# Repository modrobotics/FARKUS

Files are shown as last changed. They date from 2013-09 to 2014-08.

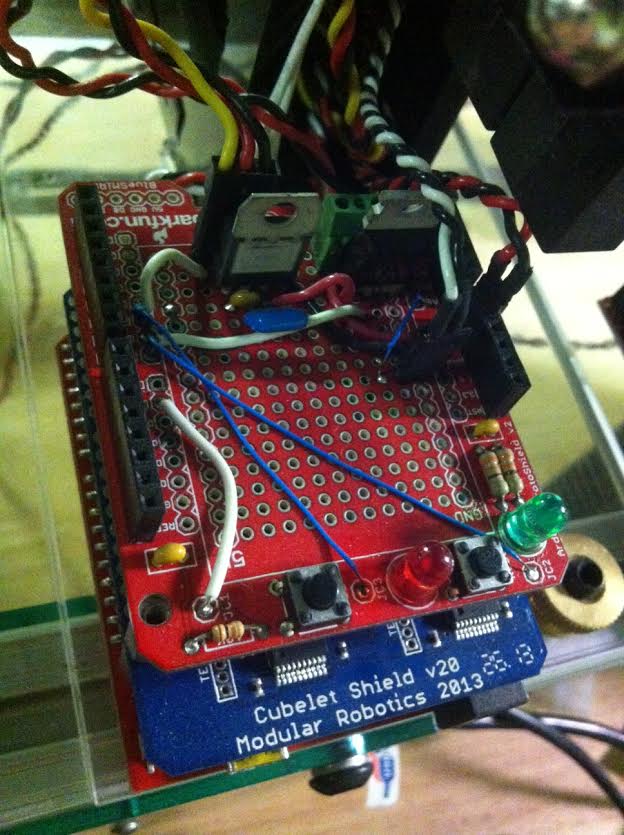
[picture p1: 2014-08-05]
FARKUS Bench/Modules/Comm Tester/Electronics/comm-board.jpg

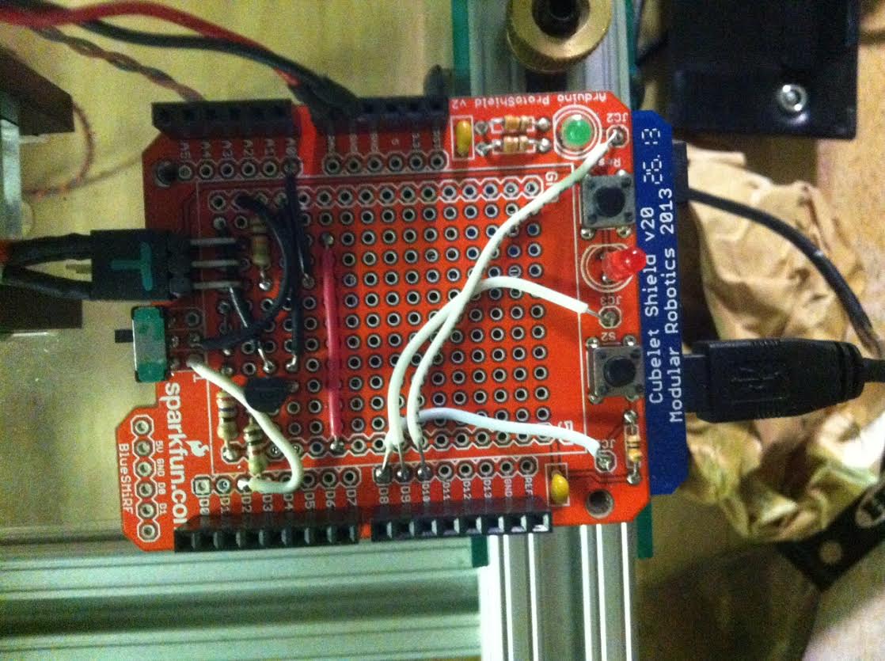
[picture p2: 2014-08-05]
FARKUS Bench/Modules/Flashlight-Brightness Module/Electronics/FBM-board.jpg

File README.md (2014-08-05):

FARKUS is an open source robotic construction kit for factory automation.
======

At Modular Robotics, we make robot construction kits for kids in our factory in Boulder, CO. Lots of people think this is batshit-crazy; toys are made in China. In order to stay cost-competitive, we do a lot of robotization and automation, but not just by buying a bunch of robot arms. Instead of buying hundred thousand dollar industrial robots and PLCs, we've been making our own industrial robots with 3D printed and laser cut parts and Arduinos.

FARKUS is more than an assembly robot, it's an ecosystem of simple robots that work together. In the same way that our commercial products are made out of lots of tiny robots, the power of FARKUS lies in the modularity and interconnection between various modules that can be reconfigured quickly to support different assembly processes and production lines.

At a basic level, a factory performs a bunch of operations to a bunch of products. The Modular Robotics factory, for instance, uses operations like soldering, ultrasonic welding, programming, testing, and printing to make products like Cubelets and MOSS. FARKUS consists of several parts: movers, to move products through the factory; a collection of modules that perform operations to the products; a control system to manage the ecosystem; and nests to cradle the products as they make their way through a production line.

This repository is pretty rough -- we've dumped files here with only minimal documentation.  We'll update as we make progress and we hope that others will contribute and document.  For now, there are a bunch of Solidworks, Eagle, and code files to peruse along with a few readmes.

More info and media on the wiki at: www.farkus.org

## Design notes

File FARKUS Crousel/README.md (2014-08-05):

FARKUS Crousel
======

The Crousel is a mechanism for pogo-testing and/or programming 60 small circuit boards without human intervention.

The hardware folder contains the master solidworks assembly (master.sldasm) which references all other solid parts.

The software folder contains the arduino sketch for the crousel and the firmware for an example flashing module.

The electronics folder contains a fritzing diagram for wiring up a crousel and an example layout for a flashing module.

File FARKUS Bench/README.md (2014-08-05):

FARKUS Bench
======

The FARKUS Bench is an assembly of interconnected modules that work together to complete a set of tasks. We use the Bench to test Cubelets.

The Bench comprises the physical Table, the Conveyance, and Modules, along with the Cubelet Holder (which is a type of FARKUS Nest) and some electrical interfaces.

The Table is the mechanical substrate to which Modules and the Conveyance are fixed. Modules are the units that perform tasks, and the Conveyance is a device that advances workpieces (Cubelets, in our case) through the Modules. The Cubelet Holder is a Nest that has been specifically designed to attach Cubelets to the Conveyance, and the electrical interfaces allow Modules to easily connect up to the Table and communicate with one another.

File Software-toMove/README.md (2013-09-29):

FARKUS Desk
======

This software supports Modular Robotics' FARKUS Table.  It is designed to be
run on a Raspberry Pi, and has been optimized for use on that platform.  That
said, all of the code is cross-platform compatible and (with some minor modifications*)
you'll be running on Windows.

Assuming you're not trying to state your love for Windows by using an open source
factory automation project, here's how you'll get your Pi set up to use FARKUS Desk.

1. Start from a vanilla distro of Raspbian.  Download from: http://downloads.raspberrypi.org/raspbian_latest 
2. Get apt-get up-to-date:
        
        sudo apt-get update
        
3. Install wxPython 2.8 for Python 2.7 (Python 2.7 itself is installed by default):
        
        sudo apt-get install python-wxgtk2.8 python-wxtools wx2.8-i18n libwxgtk2.8-dev
        
4. Install pyserial.

        cd ~
        wget https://pypi.python.org/packages/source/p/pyserial/pyserial-2.6.tar.gz
        tar -xvf pyserial-2.6.tar.gz
        cd pyserial-2.6
        python ./setup.py install
        
5. Install git

        sudo apt-get install git
        ssh key-gen -t rsa -C "[your email here]"
        
6. There are some statically-defined file paths in this code.  Please clone this repo to ```/home/pi/FARKUS```

        cd /home/pi
        git clone https://github.com/modrobotics/FARKUS.git
        
7. Adjust permissions to allow execution

        sudo chmod o+x /home/pi/FARKUS/python/FarkusDesk.py
        
8. Run Desk.

        /home/pi/FARKUS/run.exe
        
9. Profit!

* The cross-platform capability of the serial device discovery functionality
  is currently statically coded to support UNIX/Mac.  Some commenting/uncommenting
  is all that is required to switch to Windows.

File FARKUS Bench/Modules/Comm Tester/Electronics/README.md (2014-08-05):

Comm board
======
This simple board provides utility functions for the Cubelet communication test. Two MOSFET switch circuits are used to control two pneumatic solenoids that raise and lower the arm. The board also breaks out power connections and servo connections for the end-effector servos.

The two buttons are included in the Sparkfun protoshield kit. One button is used as a reset, the other button starts the test manually. The red and green LEDs indicate fail or pass result of most recent test.

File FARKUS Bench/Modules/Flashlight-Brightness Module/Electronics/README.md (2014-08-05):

FBM-board
======
This is a photograph of the prototype board for the flashlight-brightness tester. This circuit is relatively simple, comprising:
-A switch, to manually swap between flashlight and brightness modes (this is also switchable using serial comm)
-A voltage divider circuit including the photocell to measure flashlight brightness
-A BJT circuit to switch the ultra-bright LED used to test the brightness cubelet.

The two buttons are included with the protoshield kit. One is used as a reset button, the other is to manually start the test. The red and green LEDs indicate fail or pass result of most recent test.

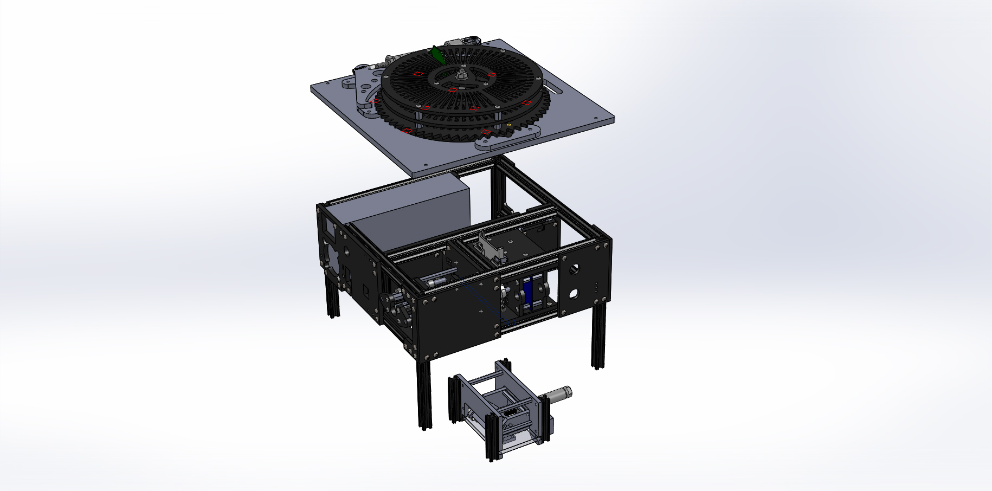
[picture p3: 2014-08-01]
FARKUS Crousel/Hardware/Images/Explode1.JPG

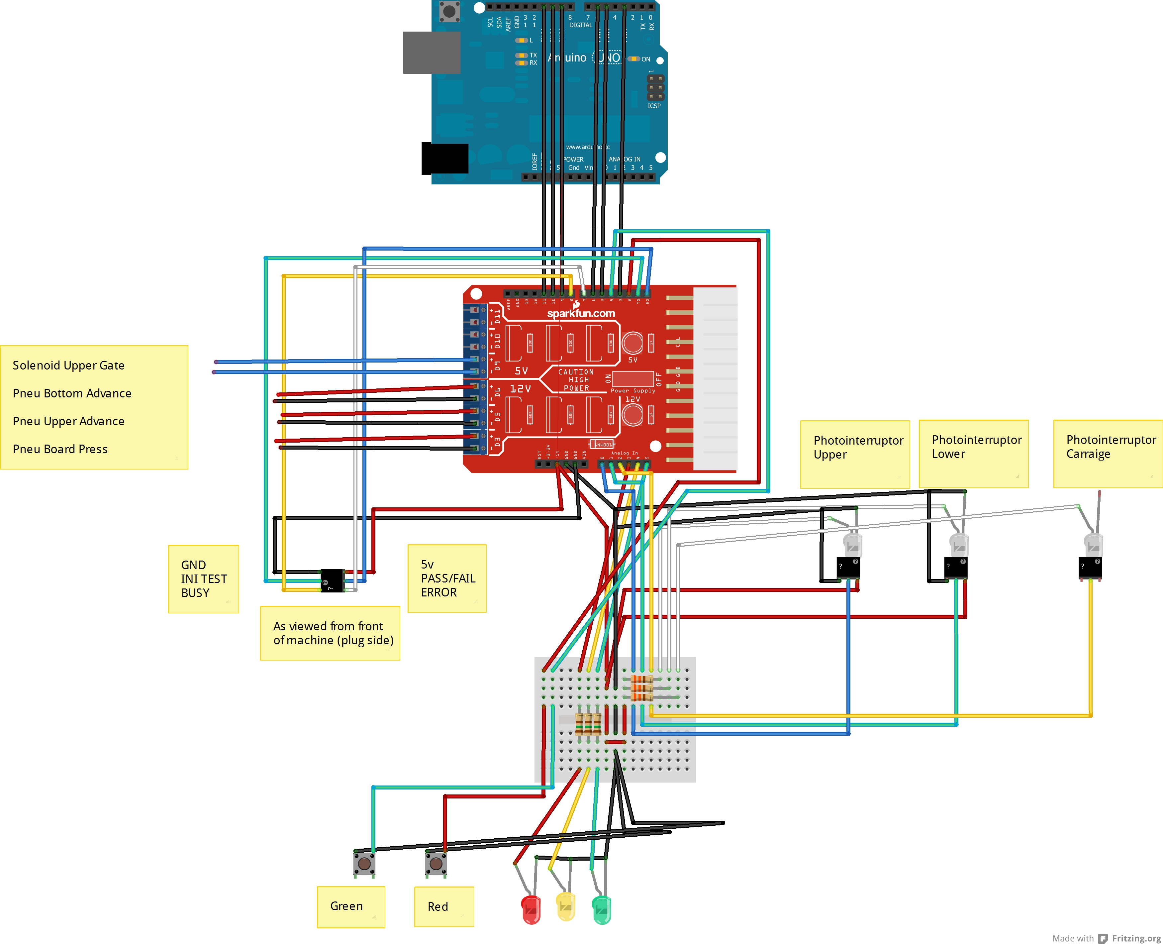
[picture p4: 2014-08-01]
FARKUS Crousel/Hardware/Images/Schematic.jpg

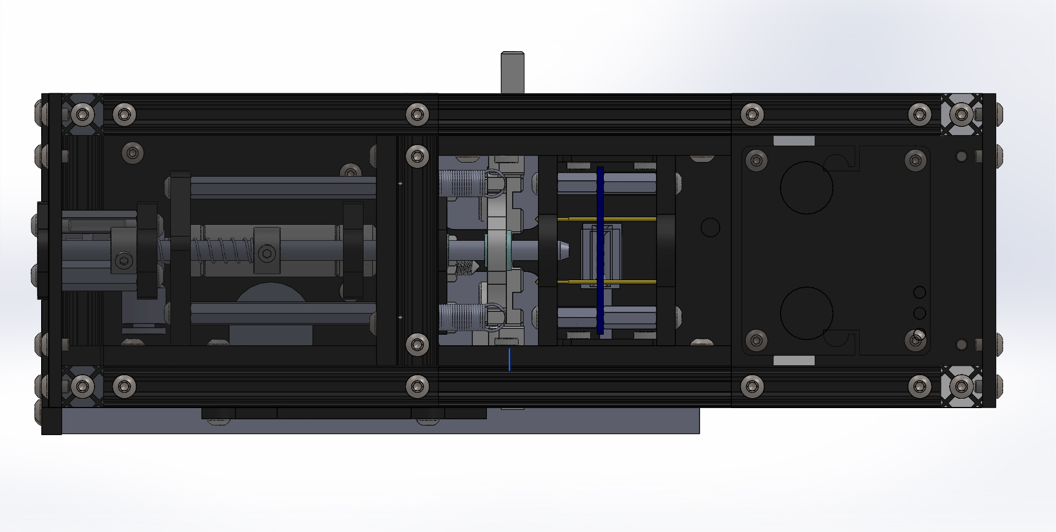
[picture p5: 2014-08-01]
FARKUS Crousel/Hardware/Images/Main1.JPG

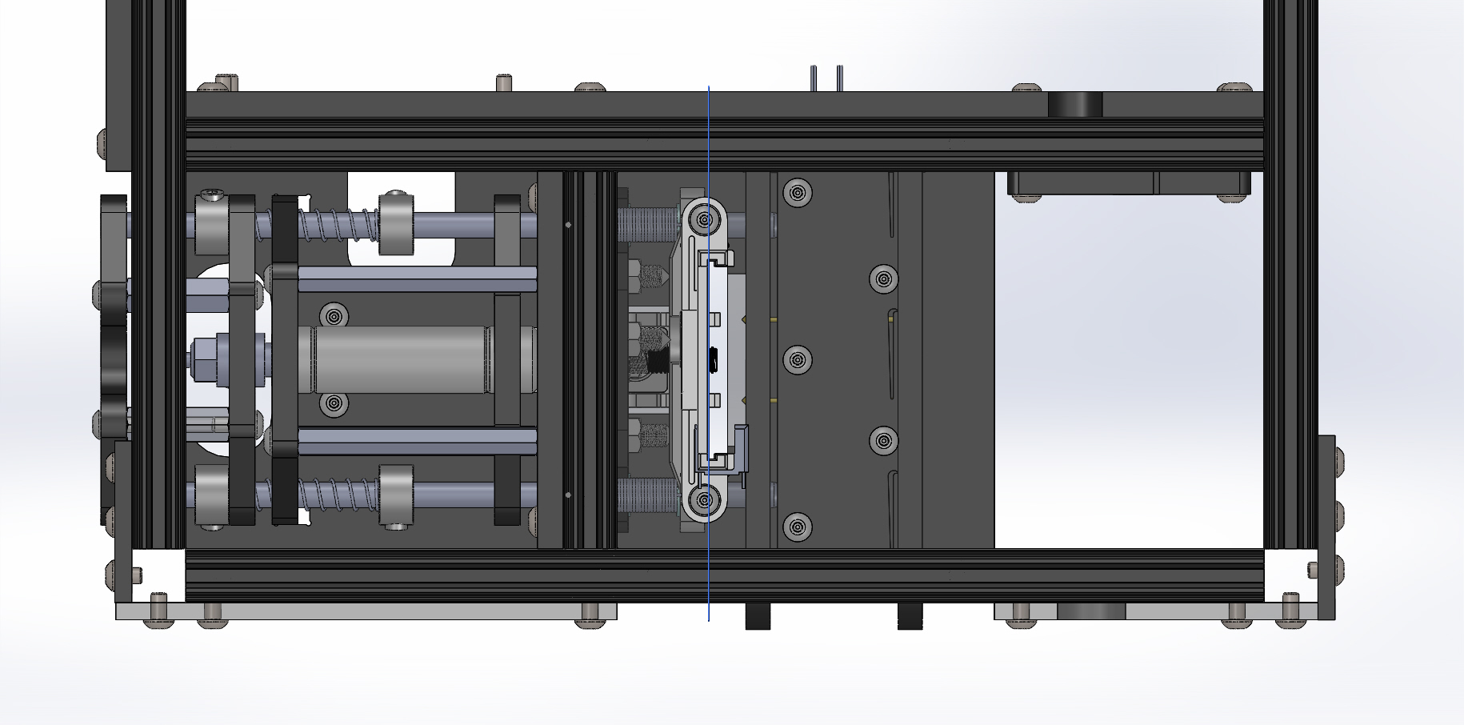
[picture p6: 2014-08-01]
FARKUS Crousel/Hardware/Images/Main2.JPG

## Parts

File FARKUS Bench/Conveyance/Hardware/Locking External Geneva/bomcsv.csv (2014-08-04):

ITEM NO. | PART NUMBER | DESCRIPTION | QTY.
1 | genevaSprocket |  | 2
2 | lockCrank |  | 2
3 | lockWheel |  | 2
4 | driveCrank |  | 1
5 | frontPlate |  | 1
6 | 57155K305 |  | 4
7 | fenderShim-0.025 |  | 8
8 | 97395A410 |  | 2
9 | 93365A110 |  | 4
10 | 90273A070 |  | 4
11 | 97395A401 |  | 4
12 | longBearing | McMaster Part # 6621K75 | 1
13 | 99040A510 | McMaster Part # 93268A509 | 2
14 | wheelSpacer |  | 2
15 | 94773A770 |  | 2
16 | 93985A534 |  | 2
17 | 92474A117 |  | 1
18 | 91124A160 |  | 2
19 | MirrorfrontPlate |  | 1
20 | 94035A581 |  | 1
21 | 93298A108 |  | 1
22 | Inch - Spur gear 24DP 66T 14.5PA 0.125FW ---S66N3.0H2.0L0.1875N |  | 1
23 | Inch - Spur gear 24DP 24T 14.5PA 0.125FW ---S24N3.0H2.0L0.1875N |  | 1
24 | 2453K31 |  | 1
25 | 91780A167 |  | 2
26 | 92474A456 |  | 1
27 | 90275A192 |  | 2
28 | 92949A111 |  | 4
29 | HX-SHCS 0.073-72x0.5x0.5-N |  | 3
30 | 1103 | Pololu Part # 1103: 29:1 Metal Gearmotor 37Dx52L mm | 1
31 | motorMountPlate |  | 1
32 | 91780A162 |  | 3
33 | 92949A106 |  | 15
34 | 92949A108 |  | 3
35 | 91239A113 |  | 6
36 | Final |  | 1
37 | RS485Breakout |  | 1
38 | 93365A120 |  | 8
39 | 93505A430 |  | 8
40 | Part26^HDLayout |  | 1

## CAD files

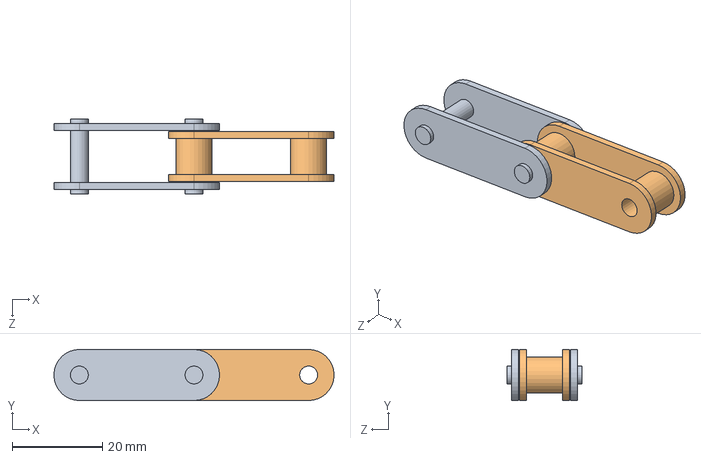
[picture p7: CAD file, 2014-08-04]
FARKUS Bench/Conveyance/Hardware/Locking External Geneva/Chain/linkPair.SLDASM
62.1 x 11.3 x 16.5 mm
bigLink
smallLink

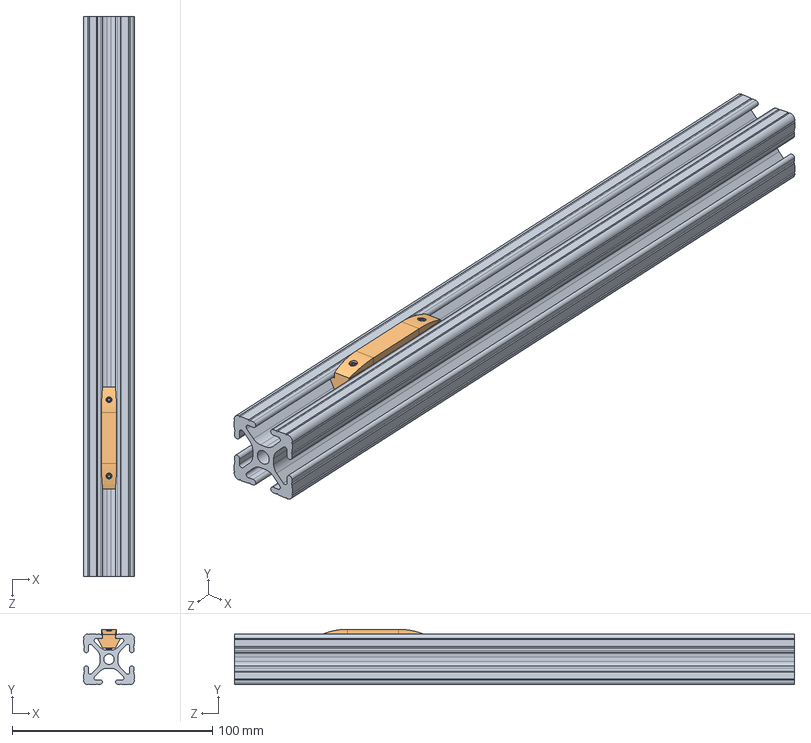
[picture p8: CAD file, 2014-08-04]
FARKUS Bench/Conveyance/Hardware/Riser/riserwithbeam.SLDASM
25.4 x 27.7 x 279.4 mm
47065T209-4SS-11IN
92395A315 x 2
94355A141 x 2

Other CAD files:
FARKUS Bench/Conveyance/Hardware/Locking External Geneva/MirrorFinal.sldasm
FARKUS Bench/Conveyance/Hardware/Locking External Geneva/User Library-QFN32 (FTDI)_Default_1.sldasm
FARKUS Bench/Conveyance/Hardware/Locking External Geneva/User Library-ALU-D8_Default_1.sldasm
FARKUS Bench/Conveyance/Hardware/Locking External Geneva/1103.SLDPRT
FARKUS Bench/Conveyance/Hardware/Locking External Geneva/3088A429.SLDPRT
FARKUS Bench/Conveyance/Hardware/Locking External Geneva/57155K305.SLDPRT
FARKUS Bench/Conveyance/Hardware/Locking External Geneva/57485K660.SLDPRT
FARKUS Bench/Conveyance/Hardware/Locking External Geneva/6409K150.SLDPRT
FARKUS Bench/Conveyance/Hardware/Locking External Geneva/90273A070.SLDPRT
FARKUS Bench/Conveyance/Hardware/Locking External Geneva/90274A126.SLDPRT
FARKUS Bench/Conveyance/Hardware/Locking External Geneva/90275A192.SLDPRT
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

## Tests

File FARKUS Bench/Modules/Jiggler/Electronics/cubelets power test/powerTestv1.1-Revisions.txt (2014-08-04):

screw terminal silkscreen must be moved

optical relay land pattern must be narrowed

arduino shield silkscreen must be moved on side with power resistor

add status LEDs for power on and each face active.

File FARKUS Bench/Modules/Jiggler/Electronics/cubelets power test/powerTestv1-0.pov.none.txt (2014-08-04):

Parts not found in 3dpack.dat or 3dusrpac.dat are:
//D1	B340A	B340A
//L1	ELL6UH120M	ELL6UH120M
//R1	6.6	AXIAL-0.8
//R2	1k	0603-RES
//R3	1k	0603-RES
//R4	1k	0603-RES
//R5	1k	0603-RES
//R6	TRIMPOT-2	TRIMPOT_TC33
//TP1	TEST-POINT3X5	PAD.03X.05
//U$3	ARDUINO_R3_SHIELD	UNO_R3_SHIELD
//U1	SI1553DL-T1-GE3	SOT65P210X110-6N
//U2	SI1553DL-T1-GE3	SOT65P210X110-6N
//U3	SI1553DL-T1-GE3	SOT65P210X110-6N
//U4	SI1553DL-T1-GE3	SOT65P210X110-6N
//U5	SI1553DL-T1-GE3	SOT65P210X110-6N
//U6	LM311DG	SOIC127P600X175-8N
//U7	FAN8303MX	FAN8303MX

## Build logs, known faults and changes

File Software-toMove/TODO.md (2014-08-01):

MUST HAVE TODO
#######################
*Proper response handling on serial workers, sending back error code (Moyes)
*Dumb emercency stop (Moyes) - Part received. 
*Hookup "parts" type menu (Moyes)
*Flashing modules final bugfix(s)  (Moyes)
*Automatic advance / preventing premature advancement (Moyes)
*Arm position detection, state status reporting (Nev)
*3D print 12 more part faces (Nev)
*~~fix double "GO" command bug~~ 
...then...

*characterize test: power (

++++++++++++++++++++++++
*smart emergency stop
*Update cubelets shieild
*Mechanical safety: EStop buttons, pinch point elimination/covers
*failure mode tracking
*make spare faces
*maintenance schedule: Tracking, alerts
touch screen

MISC TODO
########################

*Known issue: if only conveyance is connected, you won't be able to get to the
    conveyance's config window. which is fine, since there's nothing to do in there anyway
    
*FarkusTable state control system
*Functions to support  farkustesttype, required tests, etc
   - Control Module Actions
   - Update part status after
   - 
*Look for TODOs in code. Duh.
*Enums for Commands
*implement commands to getCurrentConfigState on modules
*Manager class/functions in FarkusTable to manage module location constraints (2 modules in 1 location, etc.)
*Click on part-> Part details window with tests to run, results, serial number, added date/time, etc
*Click on module-> Module details, config.  WE have basic config.  Add buttons/text for manual commands, status debug info
*Ensure everything is properly destroy()'d before close()---memory leak risk
*serial failures aren't properly updating the Statusbar..fix that.

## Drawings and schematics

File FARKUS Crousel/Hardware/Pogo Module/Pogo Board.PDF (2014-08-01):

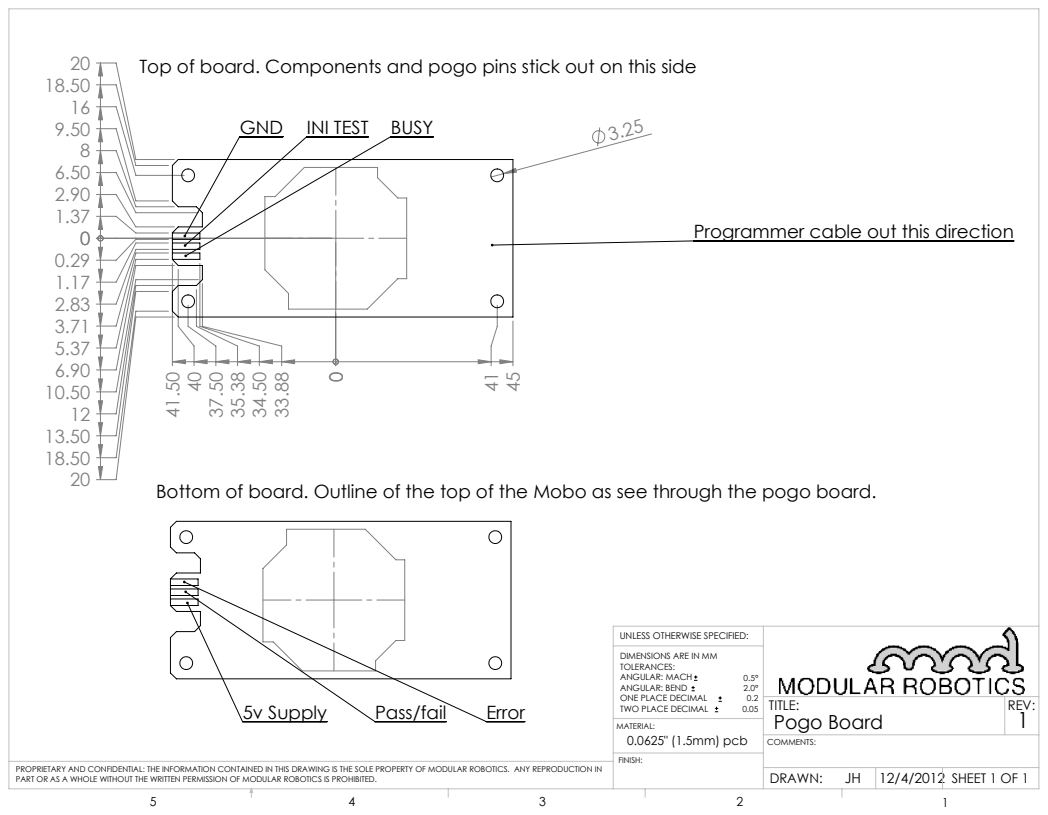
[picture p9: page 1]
5v Supply; Pass/fail; Error; Top of board. Components and pogo pins stick out on this side; SHEET 1 OF 1; DRAWN:; Pogo Board

GND INI TEST BUSY

Programmer cable out this direction

Bottom of board. Outline of the top of the Mobo as see through the pogo board.

UNLESS OTHERWISE SPECIFIED:
DIMENSIONS ARE IN MM
TOLERANCES:
ANGULAR: MACH
ANGULAR: BEND
ONE PLACE DECIMAL
TWO PLACE DECIMAL
MATERIAL:
0.0625" (1.5mm) pcb

PROPRIETARY AND CONFIDENTIAL: THE INFORMATION CONTAINED IN THIS DRAWING IS THE SOLE PROPERTY OF MODULAR ROBOTICS. ANY REPRODUCTION IN
PART OR AS A WHOLE WITHOUT THE WRITTEN PERMISSION OF MODULAR ROBOTICS IS PROHIBITED.

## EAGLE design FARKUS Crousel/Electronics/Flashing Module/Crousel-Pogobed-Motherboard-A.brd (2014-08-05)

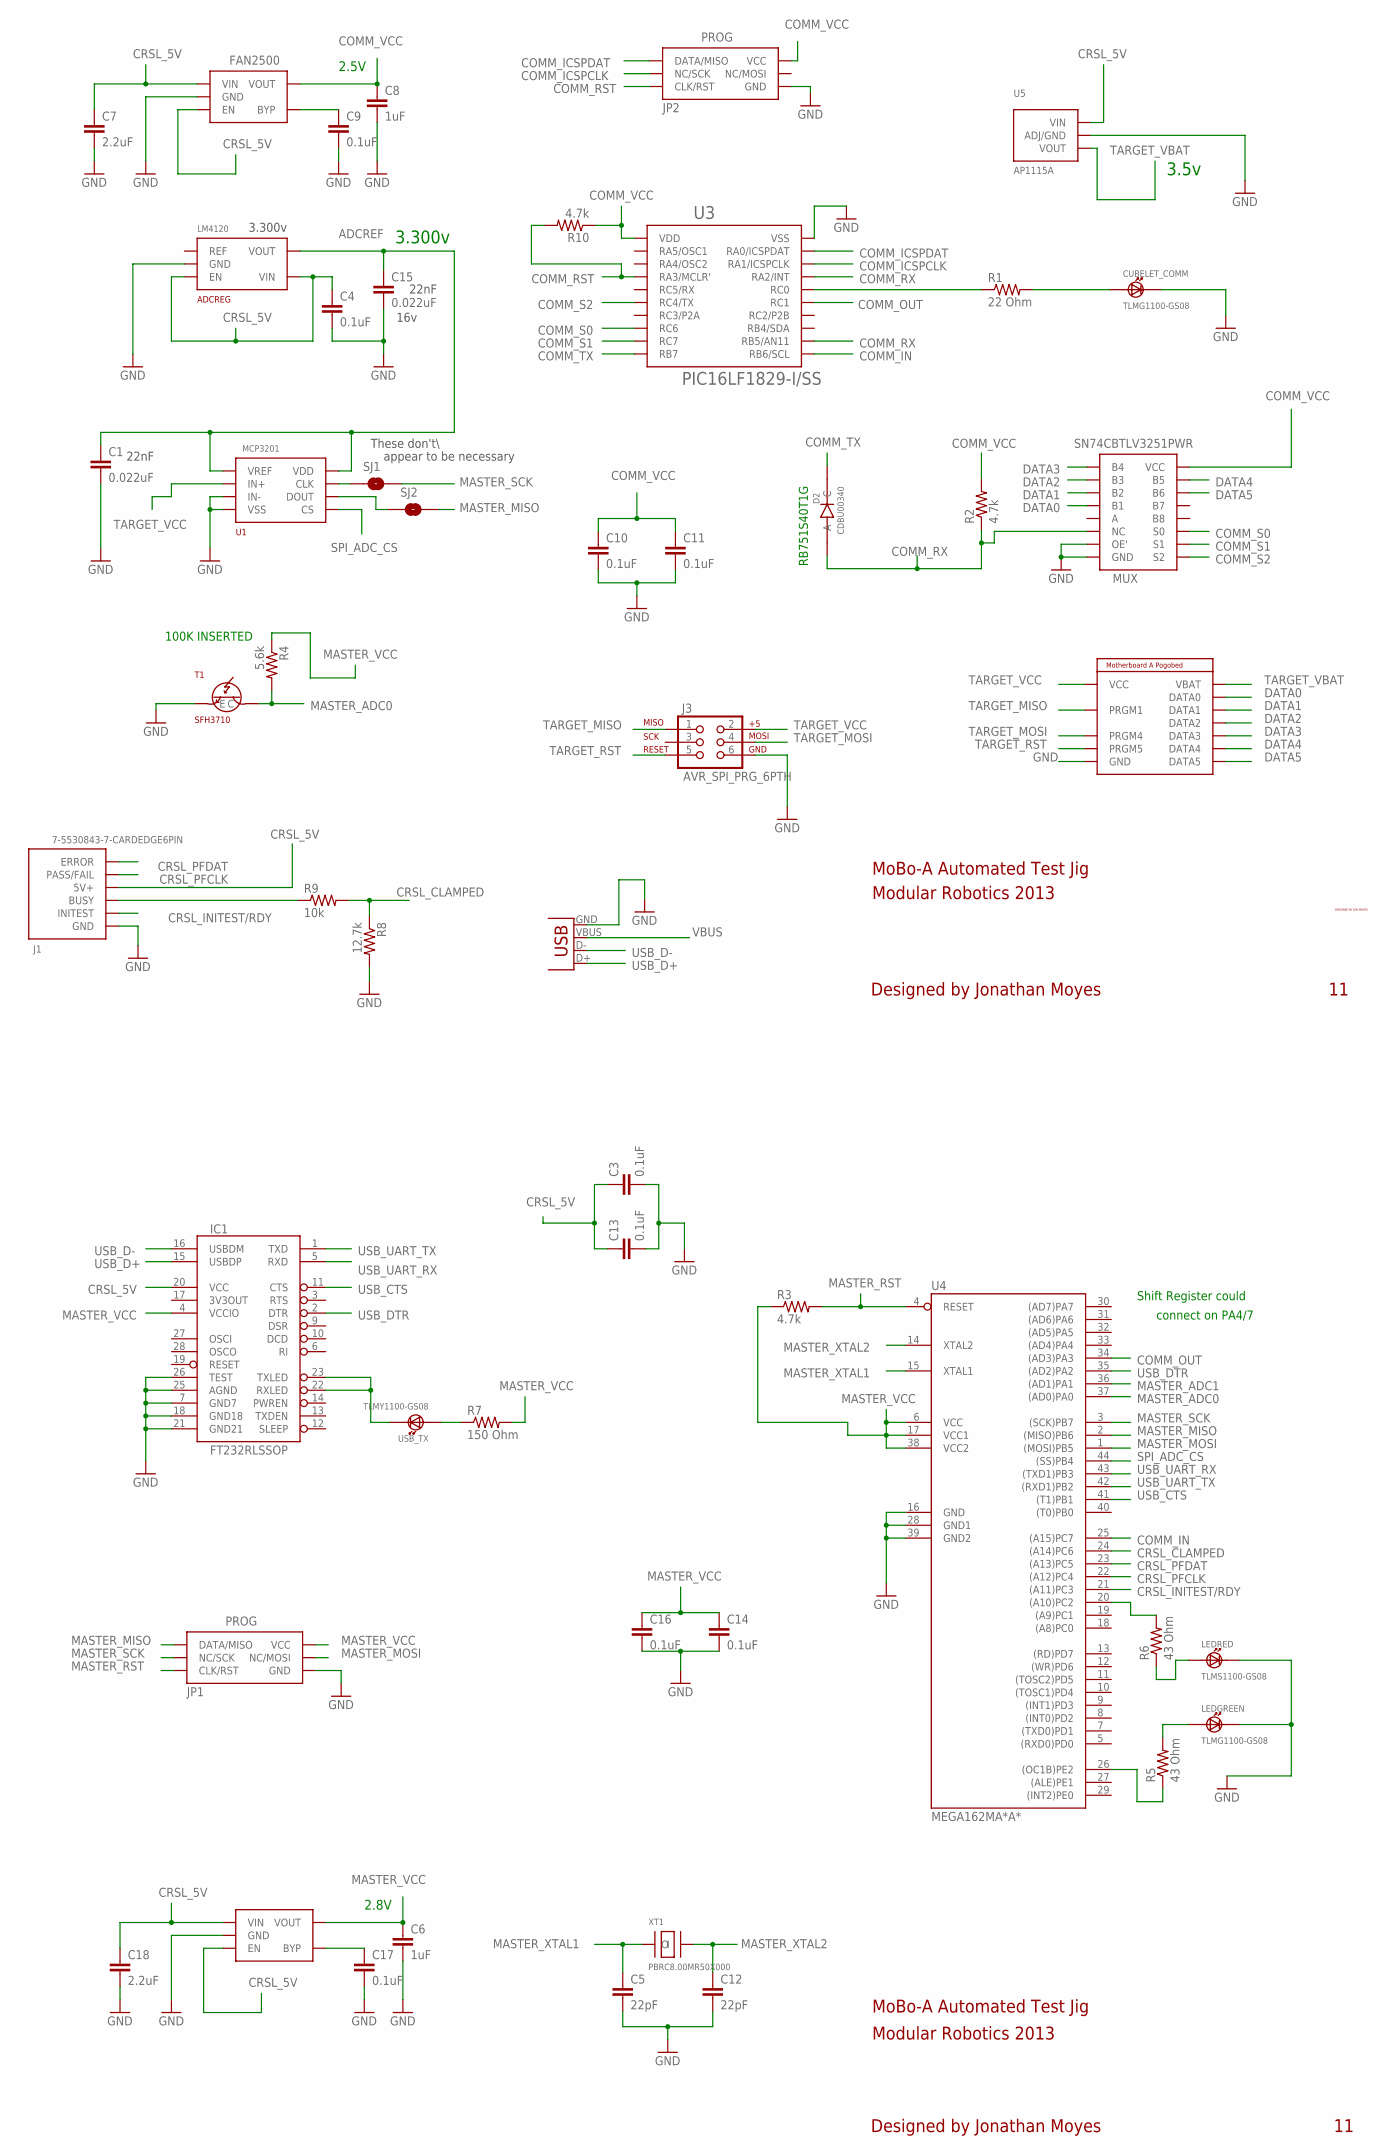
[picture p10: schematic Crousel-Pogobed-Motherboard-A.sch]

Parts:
2.8V: FAN2500
ADCREG: LM4120
C1, C15: 0.022uF; 0402-CAP
C3, C4, C9, C10, C11, C13, C14, C16, C17: 0.1uF; 0402-CAP
C5, C12: 22pF; 0402-CAP
C6, C8: 1uF; 0402-CAP
C7, C18: 2.2uF; 0402-CAP
COMMREG: FAN2500
CUBELET_COMM: TLMG1100-GS08; TLM*1100-GS08
D2: CDBU00340
IC1: FT232RLSSOP; SSOP28DB
J1: 7-5530843-7-CARDEDGE6PIN
J2: MOBOA
J3: AVR_SPI_PRG_6PTH; 2X3
JP1, JP2: PROG
LEDGREEN: TLMG1100-GS08; TLM*1100-GS08
LEDRED: TLMS1100-GS08; TLM*1100-GS08
MUX: SN74CBTLV3251PWR
R1: 22 Ohm; 0402-RES
R2, R3, R10: 4.7k; 0402-RES
R4: 5.6k; 0402-RES
R5, R6: 43 Ohm; 0402-RES
R7: 150 Ohm; 0402-RES
R8: 12.7k; 0402-RES
R9: 10k; 0402-RES
SJ1, SJ2: SOLDERJUMPERNO; SJ_2S-NO
T1: SFH3710
U1: MCP3201
U3: PIC16LF1829-I/SS
U4: MEGA162MA*A*; TQFP44
U5: AP1115A; SOT89
U$1: JON_MOYES_SIGNATURE
USB_TX: TLMY1100-GS08; TLM*1100-GS08
X1: USBPTH; USB-B-PTH
XT1: PBRC8.00MR50X000

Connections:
ADCREF: ADCREG.P$5 (VOUT), C1.1, C15.1, U1.P$1 (VREF), U1.P$8 (VDD)
COMM_ICSPCLK: JP2.P$3 (NC/SCK), U3.P$18 (RA1/ICSPCLK)
COMM_ICSPDAT: JP2.P$1 (DATA/MISO), U3.P$19 (RA0/ICSPDAT)
COMM_IN: U3.P$11 (RB6/SCL), U4.25 ((A15)PC7)
COMM_OUT: U3.P$15 (RC1), U4.34 ((AD3)PA3)
COMM_RST: JP2.P$5 (CLK/RST), R10.2, U3.P$4 (RA3/MCLR')
COMM_RX: D2.P$2 (A), MUX.P$6 (NC), R2.1, U3.P$12 (RB5/AN11), U3.P$17 (RA2/INT)
COMM_S0: MUX.P$11 (S0), U3.P$8 (RC6)
COMM_S1: MUX.P$10 (S1), U3.P$9 (RC7)
COMM_S2: MUX.P$9 (S2), U3.P$6 (RC4/TX)
COMM_TX: D2.P$1 (C), U3.P$10 (RB7)
COMM_VCC: C8.1, C10.1, C11.1, COMMREG.P$5 (VOUT), JP2.P$2 (VCC), MUX.P$16 (VCC), R2.2, R10.1, U3.P$1 (VDD)
CRSL_5V: 2.8V.P$1 (VIN), 2.8V.P$3 (EN), ADCREG.P$3 (EN), ADCREG.P$4 (VIN), C3.1, C4.1, C7.1, C13.1, C18.1, COMMREG.P$1 (VIN), COMMREG.P$3 (EN), IC1.20 (VCC), J1.P$4 (5V+), U5.3 (VIN)
CRSL_CLAMPED: R8.1, R9.2, U4.24 ((A14)PC6)
CRSL_INITEST/RDY: J1.P$2 (INITEST), U4.21 ((A11)PC3)
CRSL_PFCLK: J1.P$5 (PASS/FAIL), U4.22 ((A12)PC4)
CRSL_PFDAT: J1.P$6 (ERROR), U4.23 ((A13)PC5)
DATA0: J2.DATA0, MUX.P$4 (B1)
DATA1: J2.DATA1, MUX.P$3 (B2)
DATA2: J2.DATA2, MUX.P$2 (B3)
DATA3: J2.DATA3, MUX.P$1 (B4)
DATA4: J2.DATA4, MUX.P$15 (B5)
DATA5: J2.DATA5, MUX.P$14 (B6)
GND: 2.8V.P$2 (GND), ADCREG.P$2 (GND), C1.2, C3.2, C4.2, C5.2, C6.2, C7.2, C8.2, C9.2, C10.2, C11.2, C12.2, C13.2, C14.2, C15.2, C16.2, C17.2, C18.2, COMMREG.P$2 (GND), CUBELET_COMM.C, IC1.7 (GND7), IC1.18 (GND18), IC1.21 (GND21), IC1.25 (AGND), IC1.26 (TEST), J1.P$3 (GND), J2.PRGM6/GND (GND), J3.6, JP1.P$6 (GND), JP2.P$6 (GND), LEDGREEN.C, LEDRED.C, MUX.P$7 (OE'), MUX.P$8 (GND), R8.2, T1.E, U1.P$3 (IN-), U1.P$4 (VSS), U3.P$20 (VSS), U4.16 (GND), U4.28 (GND1), U4.39 (GND2), U5.2 (ADJ/GND), U5.2@1 (ADJ/GND), X1.GND
LED1: R6.2, U4.20 ((A10)PC2)
MASTER_ADC0: R4.2, T1.C, U4.37 ((AD0)PA0)
MASTER_ADC1: U4.36 ((AD1)PA1)
MASTER_MISO: JP1.P$1 (DATA/MISO), SJ2.2, U4.2 ((MISO)PB6)
MASTER_MOSI: JP1.P$4 (NC/MOSI), U4.1 ((MOSI)PB5)
MASTER_RST: JP1.P$5 (CLK/RST), R3.2, U4.4 (RESET)
MASTER_SCK: JP1.P$3 (NC/SCK), SJ1.2, U4.3 ((SCK)PB7)
MASTER_VCC: 2.8V.P$5 (VOUT), C6.1, C14.1, C16.1, IC1.4 (VCCIO), JP1.P$2 (VCC), R3.1, R4.1, R7.2, U4.6 (VCC), U4.17 (VCC1), U4.38 (VCC2)
MASTER_XTAL1: C5.1, U4.15 (XTAL1), XT1.I
MASTER_XTAL2: C12.1, U4.14 (XTAL2), XT1.O
unnamed: SJ1.1, U1.P$7 (CLK)
unnamed: R1.1, U3.P$16 (RC0)
unnamed: C9.1, COMMREG.P$4 (BYP)
unnamed: CUBELET_COMM.A, R1.2
unnamed: 2.8V.P$4 (BYP), C17.1
unnamed: IC1.22 (RXLED), IC1.23 (TXLED), USB_TX.C
unnamed: R5.1, U4.26 ((OC1B)PE2)
unnamed: R7.1, USB_TX.A
unnamed: LEDGREEN.A, R5.2
unnamed: J1.P$1 (BUSY), R9.1
unnamed: SJ2.1, U1.P$6 (DOUT)
unnamed: LEDRED.A, R6.1
SPI_ADC_CS: U1.P$5 (CS), U4.44 ((SS)PB4)
TARGET_MISO: J2.PRGM1, J3.1
TARGET_MOSI: J2.PRGM4, J3.4
TARGET_RST: J2.PRGM5, J3.5
TARGET_VBAT: J2.VBAT, U5.1 (VOUT)
TARGET_VCC: J2.PRGM2/VCC (VCC), J3.2, U1.P$2 (IN+)
USB_CTS: IC1.11 (CTS), U4.41 ((T1)PB1)
USB_D+: IC1.15 (USBDP), X1.D+
USB_D-: IC1.16 (USBDM), X1.D-
USB_DTR: IC1.2 (DTR), U4.35 ((AD2)PA2)
USB_UART_RX: IC1.5 (RXD), U4.43 ((TXD1)PB3)
USB_UART_TX: IC1.1 (TXD), U4.42 ((RXD1)PB2)
VBUS: X1.VBUS

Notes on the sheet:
16v
3.300v
2.5V
RB751S40T1G
2.8V
Shift Register could
connect on PA4/7
MoBo-A Automated Test Jig
Modular Robotics 2013
Designed by Jonathan Moyes
3.5v
22nF
These don't\
appear to be necessary
100K INSERTED

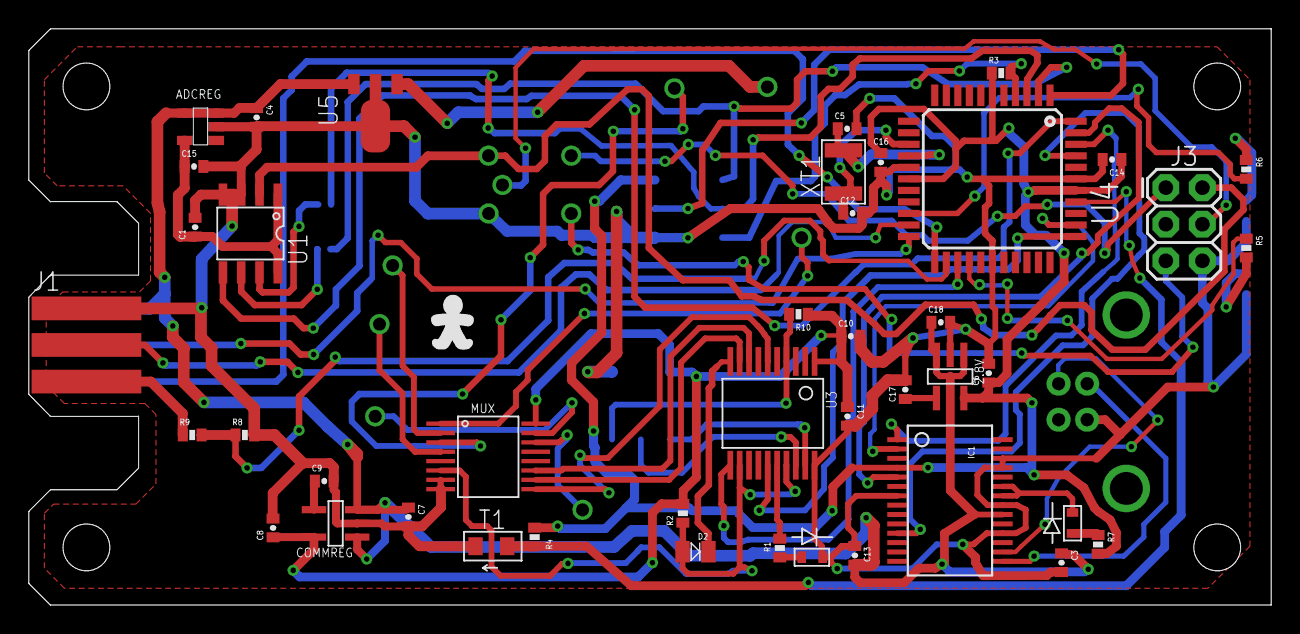
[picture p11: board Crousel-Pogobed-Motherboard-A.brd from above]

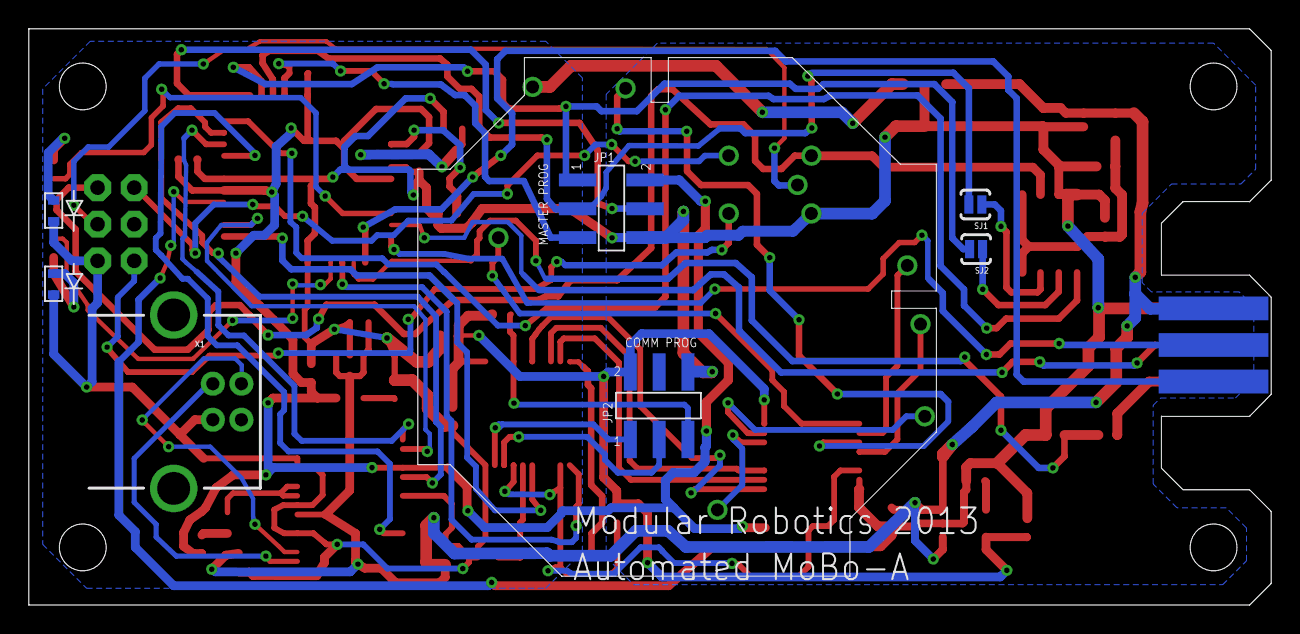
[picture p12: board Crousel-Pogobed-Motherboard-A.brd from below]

Board: 2 copper layers, 86.2 x 40.0 mm, 52 parts (8 on the bottom side), 57 nets.

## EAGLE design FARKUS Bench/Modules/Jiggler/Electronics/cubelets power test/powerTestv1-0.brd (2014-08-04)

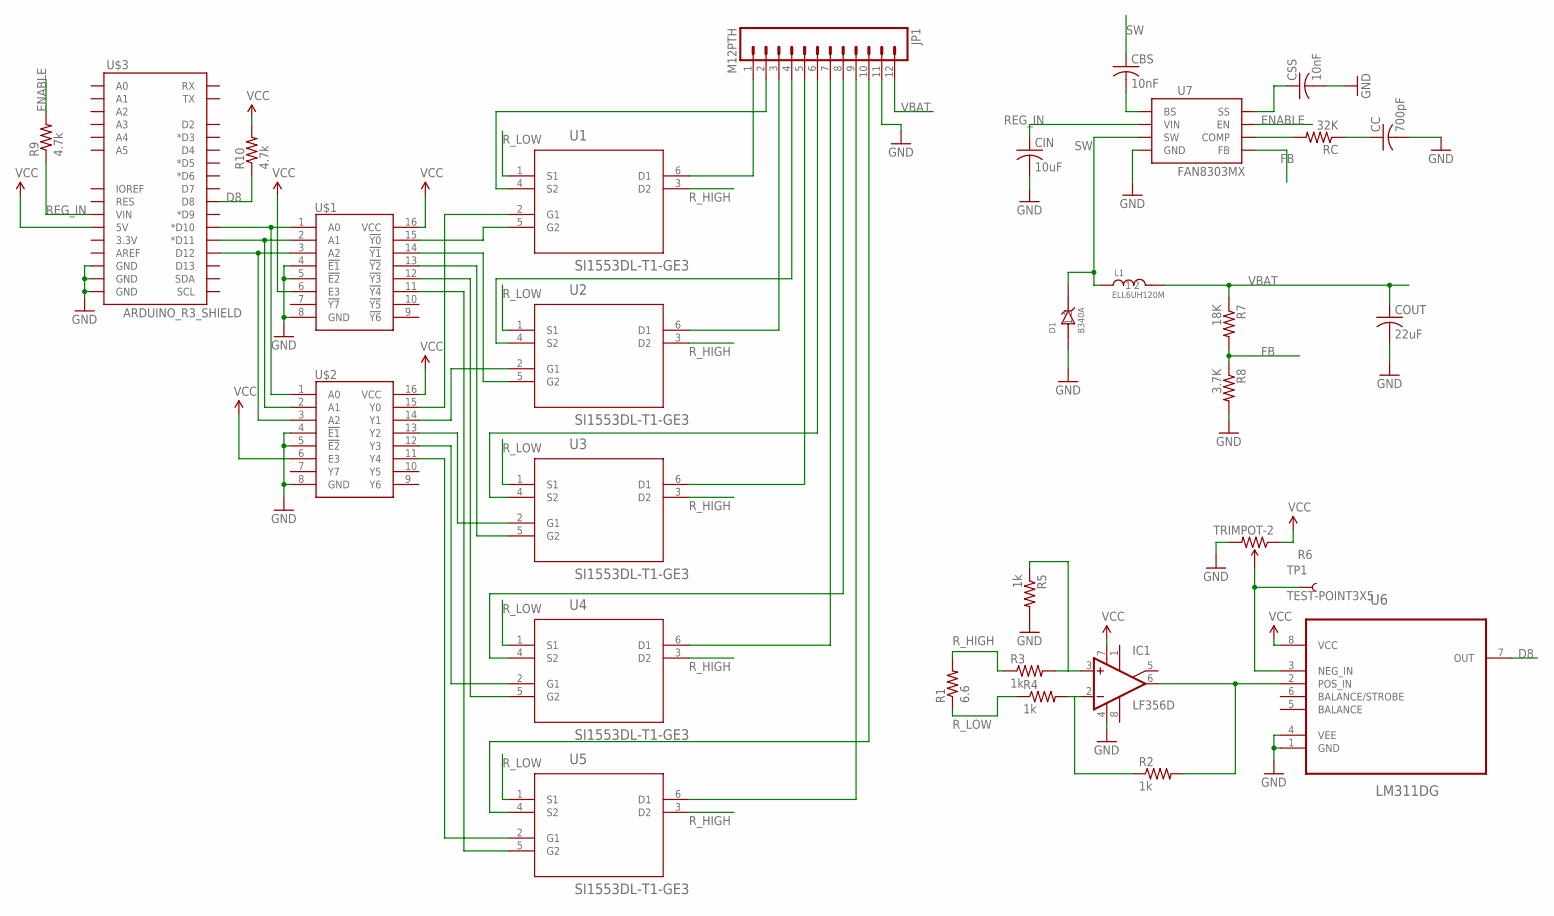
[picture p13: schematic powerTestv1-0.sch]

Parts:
CBS: 10nF; C0603
CC: 700pF; C0603
CIN: 10uF; C0603
COUT: 22uF; C0603
CSS: 10nF; C0603
D1: B340A
IC1: LF356D; SO08
JP1: M12PTH; 1X12
L1: ELL6UH120M
R1: 6.6; AXIAL-0.8
R2, R3, R4, R5: 1k; 0603-RES
R6: TRIMPOT-2; TRIMPOT_TC33
R7: 18K; R0603
R8: 3.7K; R0603
R9, R10: 4.7k; R0603
RC: 32K; R0603
TP1: TEST-POINT3X5; PAD.03X.05
U1, U2, U3, U4, U5: SI1553DL-T1-GE3; SOT65P210X110-6N
U6: LM311DG; SOIC127P600X175-8N
U7: FAN8303MX
U$1: 74HC138SO16; SO16
U$2: 74HC238SO16; SO16
U$3: ARDUINO_R3_SHIELD; UNO_R3_SHIELD

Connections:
D8: R10.1, U6.7 (OUT), U$3.D8
ENABLE: R9.2, U7.P$7 (EN)
FB: R7.2, R8.1, U7.P$5 (FB)
GND: CC.2, CIN.2, COUT.2, CSS.2, D1.P$1 (1), IC1.4 (V-), JP1.11, R5.2, R6.3 (CW), R8.2, U6.1 (GND), U6.4 (VEE), U7.P$4 (GND), U$1.4 (!E1), U$1.5 (!E2), U$1.8 (GND), U$2.4 (!E1), U$2.5 (!E2), U$2.8 (GND), U$3.GND@0 (GND), U$3.GND@1 (GND), U$3.GND@2 (GND)
unnamed: U$1.1 (A0), U$2.1 (A0), U$3.D10 (*D10)
unnamed: U$1.2 (A1), U$2.2 (A1), U$3.D11 (*D11)
unnamed: U$1.3 (A2), U$2.3 (A2), U$3.D12
unnamed: U1.5 (G2), U$1.15 (!Y0)
unnamed: U2.5 (G2), U$1.14 (!Y1)
unnamed: U3.5 (G2), U$1.13 (!Y2)
unnamed: U4.5 (G2), U$1.12 (!Y3)
unnamed: U5.5 (G2), U$1.11 (!Y4)
unnamed: U1.2 (G1), U$2.15 (Y0)
unnamed: U2.2 (G1), U$2.14 (Y1)
unnamed: U3.2 (G1), U$2.13 (Y2)
unnamed: U4.2 (G1), U$2.12 (Y3)
unnamed: U5.2 (G1), U$2.11 (Y4)
unnamed: JP1.1, U1.6 (D1)
unnamed: JP1.3, U2.6 (D1)
unnamed: JP1.5, U3.6 (D1)
unnamed: JP1.7, U4.6 (D1)
unnamed: JP1.9, U5.6 (D1)
unnamed: JP1.2, U1.4 (S2)
unnamed: IC1.2 (-IN), R2.1, R4.2
unnamed: IC1.6 (OUT), R2.2, U6.2 (POS_IN)
unnamed: JP1.4, U2.4 (S2)
unnamed: JP1.6, U3.4 (S2)
unnamed: JP1.8, U4.4 (S2)
unnamed: IC1.3 (+IN), R3.2, R5.1
unnamed: R6.2 (WIPER), TP1.P$1, U6.3 (NEG_IN)
unnamed: CSS.1, U7.P$8 (SS)
unnamed: CBS.2, U7.P$1 (BS)
unnamed: RC.2, U7.P$6 (COMP)
unnamed: CC.1, RC.1
unnamed: JP1.10, U5.4 (S2)
REG_IN: CIN.1, R9.1, U7.P$2 (VIN), U$3.VIN
R_HIGH: R1.P$2 (2), R3.1, U1.3 (D2), U2.3 (D2), U3.3 (D2), U4.3 (D2), U5.3 (D2)
R_LOW: R1.P$1 (1), R4.1, U1.1 (S1), U2.1 (S1), U3.1 (S1), U4.1 (S1), U5.1 (S1)
SW: CBS.1, D1.P$2 (2), L1.P$1 (1), U7.P$3 (SW)
VBAT: COUT.1, JP1.12, L1.P$2 (2), R7.1
VCC: IC1.7 (V+), R6.1 (CCW), R10.2, U6.8 (VCC), U$1.6 (E3), U$1.16 (VCC), U$2.6 (E3), U$2.16 (VCC), U$3.5V

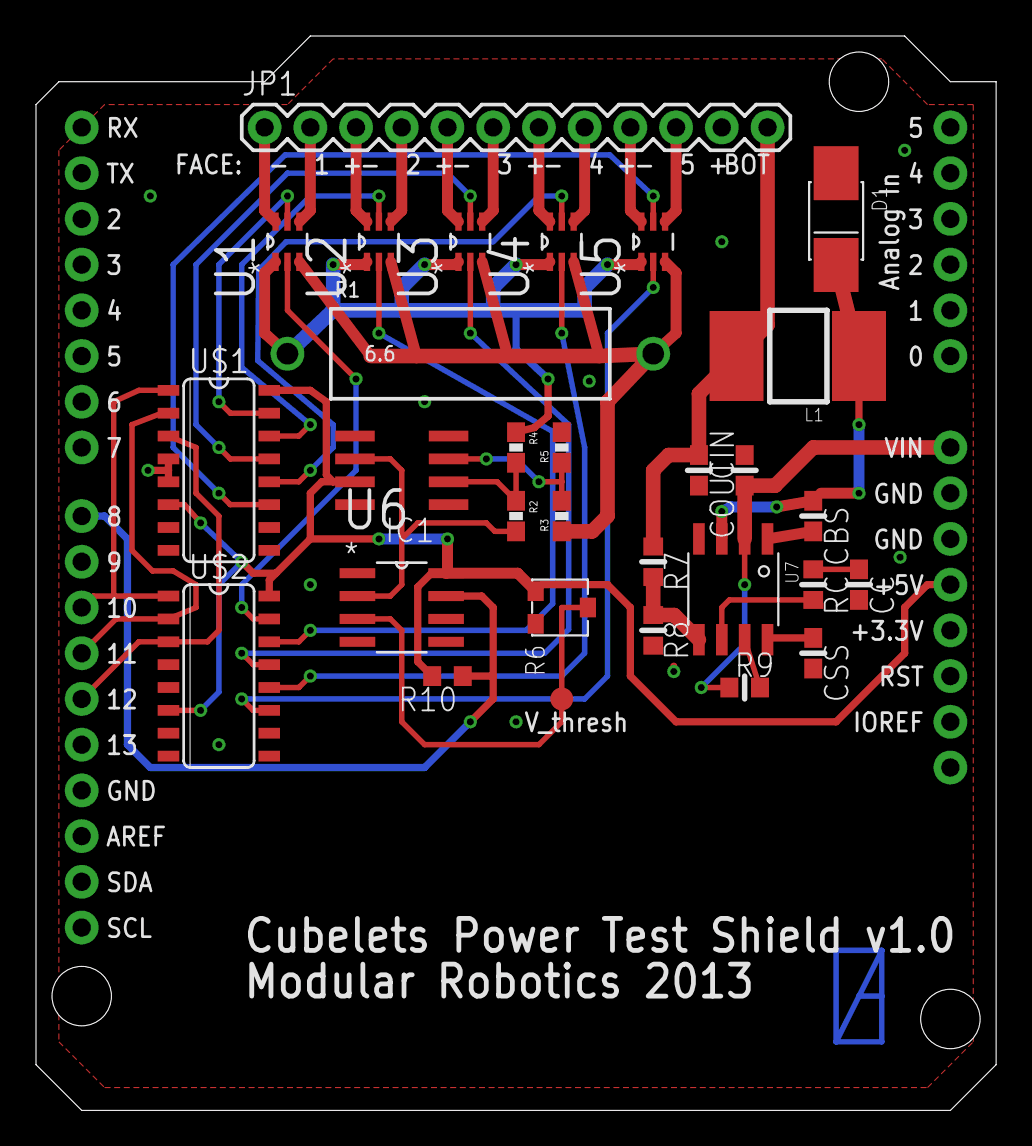
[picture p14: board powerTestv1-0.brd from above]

Board: 2 copper layers, 53.3 x 59.7 mm, 31 parts (0 on the bottom side), 41 nets.

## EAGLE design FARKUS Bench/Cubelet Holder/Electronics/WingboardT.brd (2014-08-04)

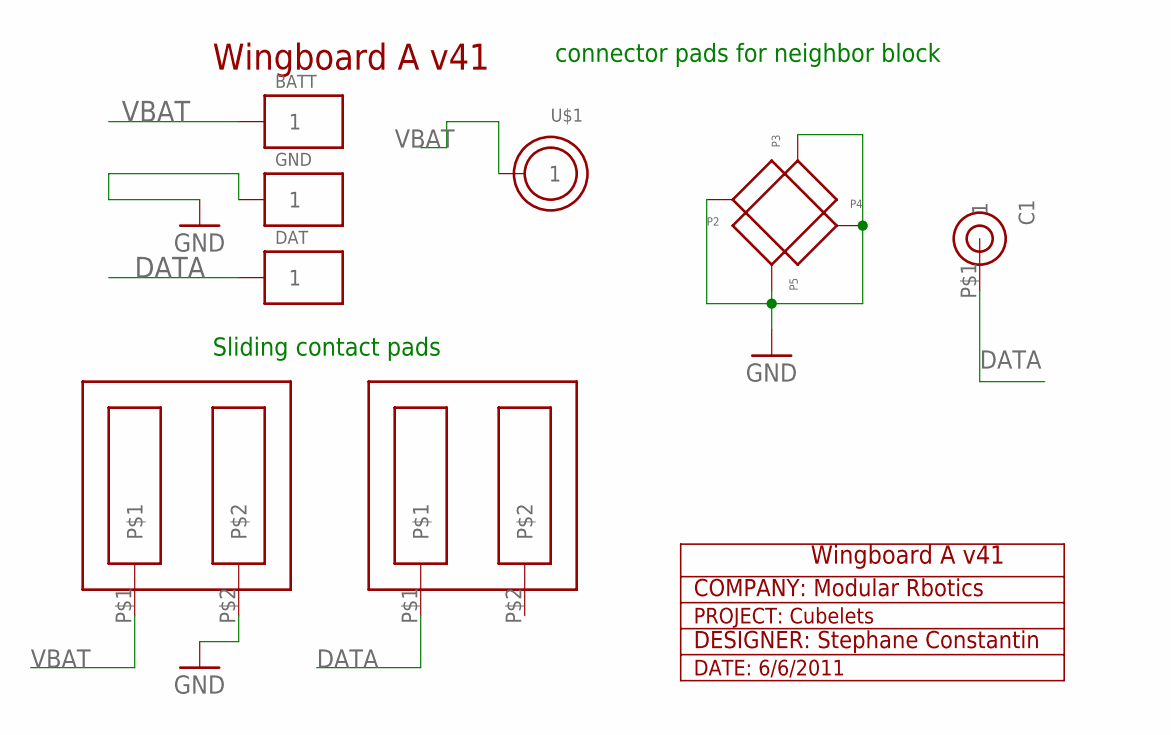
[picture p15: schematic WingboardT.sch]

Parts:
BATT: PAD2
C1: COMM_PIN2
DAT: PAD2
GND: PAD2
J1, J2: SLIDING_CONTACT
P2, P3, P4, P5: GND_PAD_WING
U$1: VBAT_CIRCLE

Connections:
DATA: C1.P$1, DAT.P$1, J2.P$1
GND: GND.P$1, J1.P$2, P2.P$1, P3.P$1, P4.P$1, P5.P$1
VBAT: BATT.P$1, J1.P$1, U$1.P$1

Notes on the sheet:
connector pads for neighbor block
COMPANY: Modular Rbotics
DESIGNER: Stephane Constantin
Wingboard A v41
PROJECT: Cubelets
DATE: 6/6/2011
Sliding contact pads

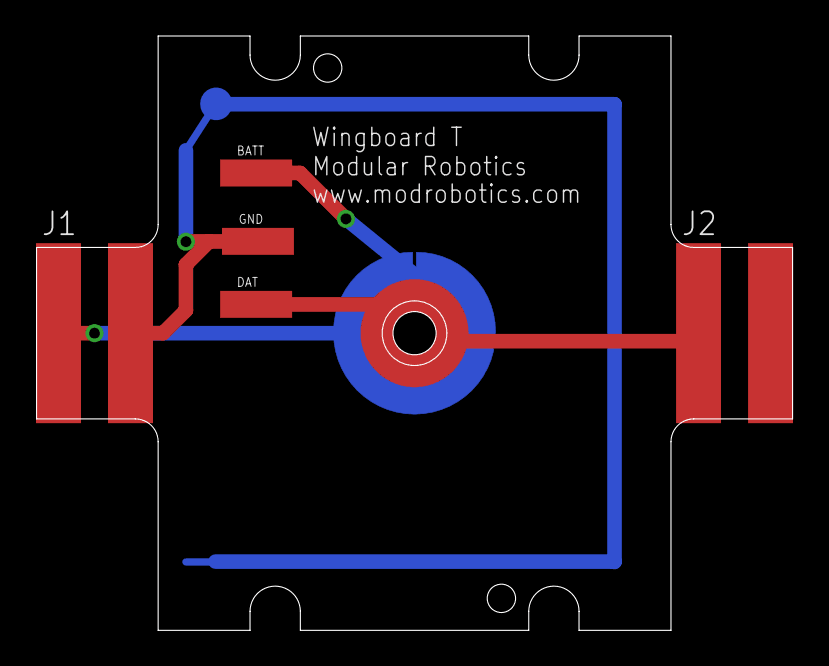
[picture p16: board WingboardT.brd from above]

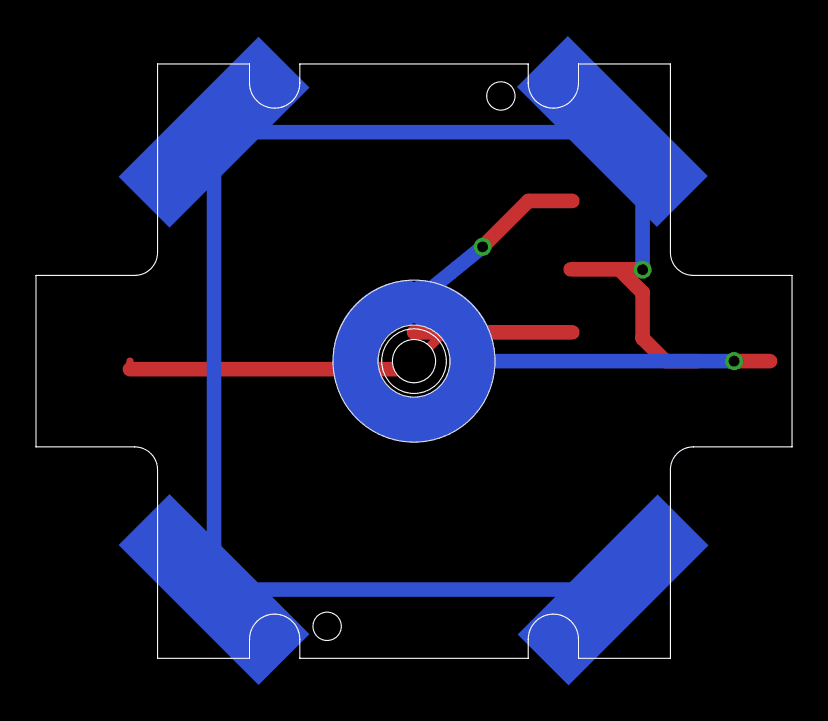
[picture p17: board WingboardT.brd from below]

Board: 2 copper layers, 42.0 x 33.0 mm, 11 parts (5 on the bottom side), 3 nets.

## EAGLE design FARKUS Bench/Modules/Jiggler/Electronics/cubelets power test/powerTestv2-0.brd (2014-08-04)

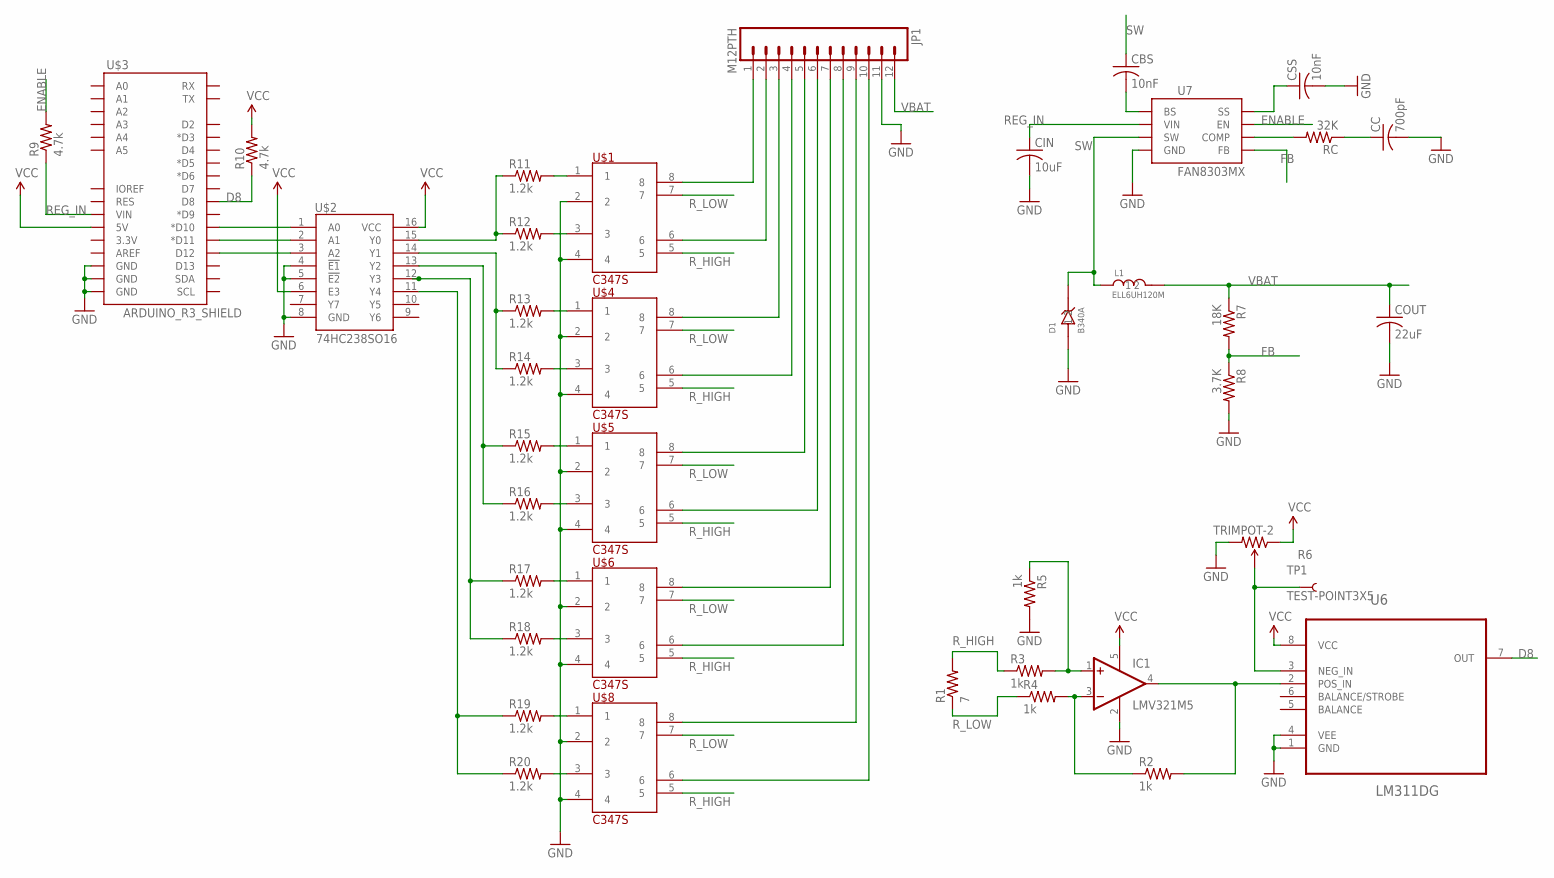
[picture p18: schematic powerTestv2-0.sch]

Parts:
CBS: 10nF; C0603
CC: 700pF; C0603
CIN: 10uF; C0603
COUT: 22uF; C0603
CSS: 10nF; C0603
D1: B340A
IC1: LMV321M5; SOT23-5
JP1: M12PTH; 1X12
L1: ELL6UH120M
R1: 7; AXIAL-0.8
R2, R3, R4, R5: 1k; 0603-RES
R6: TRIMPOT-2; TRIMPOT_TC33
R7: 18K; R0603
R8: 3.7K; R0603
R9, R10: 4.7k; R0603
R11, R12, R13, R14, R15, R16, R17, R18, R19, R20: 1.2k; 0603-RES
RC: 32K; R0603
TP1: TEST-POINT3X5; PAD.03X.05
U6: LM311DG; SOIC127P600X175-8N
U7: FAN8303MX
U$1, U$4, U$5, U$6, U$8: C347S; SOP8
U$2: 74HC238SO16; SO16
U$3: ARDUINO_R3_SHIELD; UNO_R3_SHIELD

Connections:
D8: R10.1, U6.7 (OUT), U$3.D8
ENABLE: R9.2, U7.P$7 (EN)
FB: R7.2, R8.1, U7.P$5 (FB)
GND: CC.2, CIN.2, COUT.2, CSS.2, D1.P$1 (1), IC1.2 (V-), JP1.11, R5.2, R6.3 (CW), R8.2, U6.1 (GND), U6.4 (VEE), U7.P$4 (GND), U$1.2, U$1.4, U$2.4 (!E1), U$2.5 (!E2), U$2.8 (GND), U$3.GND@0 (GND), U$3.GND@1 (GND), U$3.GND@2 (GND), U$4.2, U$4.4, U$5.2, U$5.4, U$6.2, U$6.4, U$8.2, U$8.4
unnamed: U$2.1 (A0), U$3.D10 (*D10)
unnamed: U$2.2 (A1), U$3.D11 (*D11)
unnamed: U$2.3 (A2), U$3.D12
unnamed: R12.2, U$1.3
unnamed: R14.2, U$4.3
unnamed: R15.2, U$5.1
unnamed: R16.2, U$5.3
unnamed: R11.2, U$1.1
unnamed: R17.2, U$6.1
unnamed: R18.2, U$6.3
unnamed: JP1.1, U$1.8
unnamed: JP1.2, U$1.6
unnamed: JP1.3, U$4.8
unnamed: JP1.4, U$4.6
unnamed: JP1.5, U$5.8
unnamed: JP1.6, U$5.6
unnamed: IC1.3 (-IN), R2.1, R4.2
unnamed: IC1.4 (OUT), R2.2, U6.2 (POS_IN)
unnamed: JP1.7, U$6.8
unnamed: JP1.8, U$6.6
unnamed: JP1.9, U$8.8
unnamed: IC1.1 (+IN), R3.2, R5.1
unnamed: R6.2 (WIPER), TP1.P$1, U6.3 (NEG_IN)
unnamed: CSS.1, U7.P$8 (SS)
unnamed: CBS.2, U7.P$1 (BS)
unnamed: RC.2, U7.P$6 (COMP)
unnamed: CC.1, RC.1
unnamed: JP1.10, U$8.6
unnamed: R13.2, U$4.1
unnamed: R19.2, U$8.1
unnamed: R20.2, U$8.3
unnamed: R11.1, R12.1, U$2.15 (Y0)
unnamed: R13.1, R14.1, U$2.14 (Y1)
unnamed: R15.1, R16.1, U$2.13 (Y2)
unnamed: R17.1, R18.1, U$2.12 (Y3)
unnamed: R19.1, R20.1, U$2.11 (Y4)
REG_IN: CIN.1, R9.1, U7.P$2 (VIN), U$3.VIN
R_HIGH: R1.P$2 (2), R3.1, U$1.5, U$4.5, U$5.5, U$6.5, U$8.5
R_LOW: R1.P$1 (1), R4.1, U$1.7, U$4.7, U$5.7, U$6.7, U$8.7
SW: CBS.1, D1.P$2 (2), L1.P$1 (1), U7.P$3 (SW)
VBAT: COUT.1, JP1.12, L1.P$2 (2), R7.1
VCC: IC1.5 (V+), R6.1 (CCW), R10.2, U6.8 (VCC), U$2.6 (E3), U$2.16 (VCC), U$3.5V

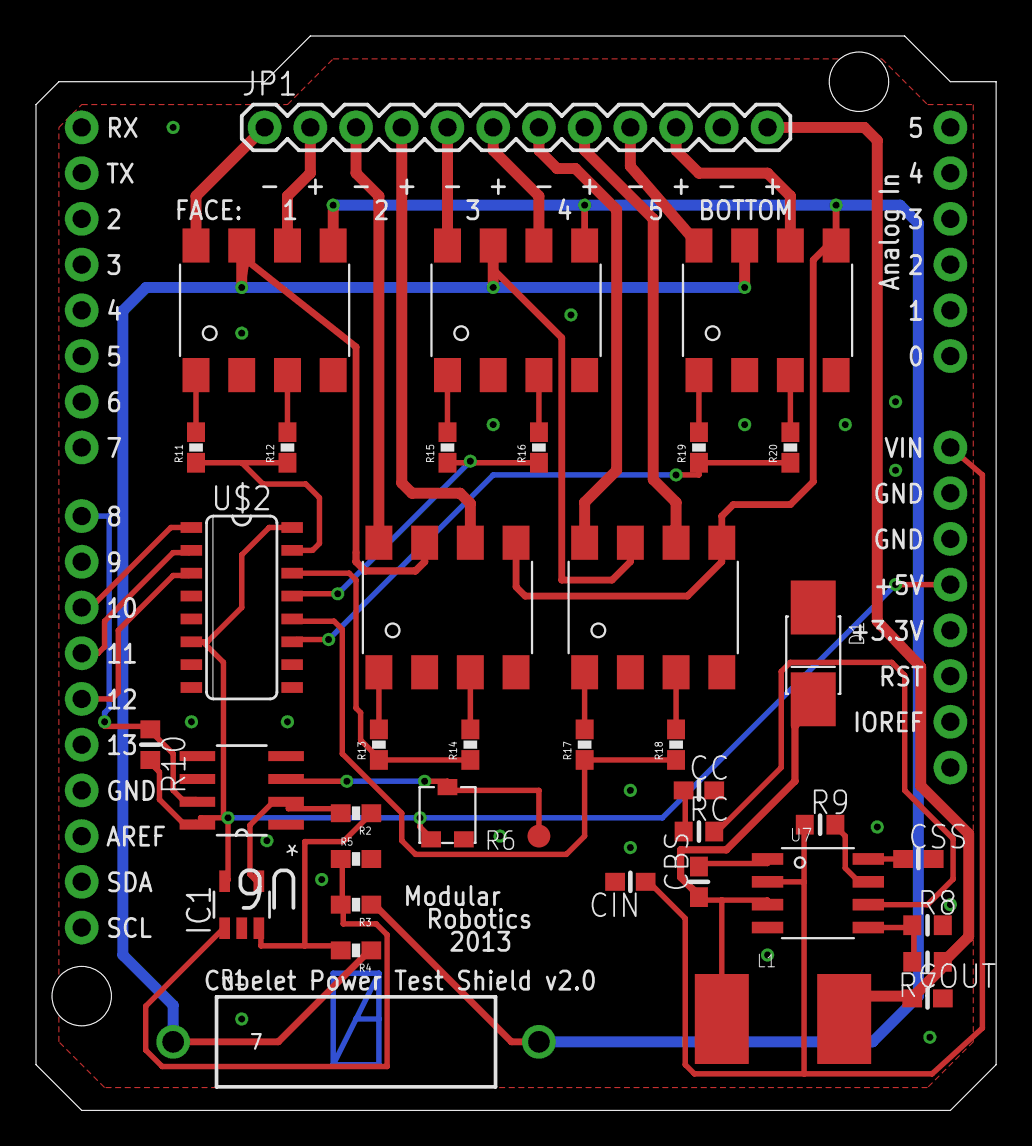
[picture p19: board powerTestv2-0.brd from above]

Board: 2 copper layers, 53.3 x 59.7 mm, 40 parts (0 on the bottom side), 46 nets.

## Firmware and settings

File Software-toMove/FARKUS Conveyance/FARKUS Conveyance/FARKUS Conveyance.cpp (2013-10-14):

/*
 * FARKUS_Conveyance.cpp
 *
 * Created: 4/9/2013 11:09:00 AM
 *  Author: Nev
 */ 
#include "Arduino.h"
#include <String.h>

#define ID "`0000" //conveyance ID string

#define MOTORENABLE 3 //motor enable pin. pull high to enable.
#define MOTOR1 4 //H-bridge input 1. 1:HIGH; 2:LOW for forward...1:LOW; 2:high for reverse. both HIGH or LOW is brake.
#define MOTOR2 5 //H-bridge input 2
#define MOTORPWM 9 //PWM pin to control motor speed
#define BREAKBEAM 6 //breakbeam sensor for geneva mechanism. is HIGH during movement, LOW when in a stable position.
#define FWDBUTTON 7 //buttons for manual operation
#define REVBUTTON 8

#define OCCLUDE_TIME 500 //time in ms to allow the geneva to occlude the sensor before error.
#define CLEAR_TIME 500 //time in ms to allow the geneva to clear the sensor before error.

void setup();
void loop();

enum State
{
	IDLE,
	WORKING,
	ERROR,
	ESTOP
	};

enum SubState
{
	WAIT,
	ACT
	};

enum Config
{
	FORWARD,
	REVERSE
	};
	
int actionResponse(String inString);

State stateVar;
SubState subStateVar;
Config configVar;

long subWaitStart = 0; //holder for the start time of a WAIT substate
long subWaitTime; //this should be set before switching to a WAIT substate to define how long (ms) to wait
bool subWaitSentinel = true; //sentinel for keeping track of first wait cycles, since the start time of a wait must be set at the first cycle
long sensorTime; //holder to keep track of sensor timing for error checking
bool firstAct = true;
bool hasOccluded = false; //sets to true once sensor is occluded
bool hasCleared = false; //sets to true once sensor is cleared

void setup()
{
	Serial.begin(9600);
	Serial.println(ID);
	pinMode(MOTORENABLE, OUTPUT);
	pinMode(MOTOR1, OUTPUT);
	pinMode(MOTOR2, OUTPUT);
	pinMode(BREAKBEAM, INPUT);
	pinMode(FWDBUTTON, INPUT);
	pinMode(REVBUTTON, INPUT);
	pinMode(MOTORPWM, OUTPUT);
	//set motor speed
	analogWrite(MOTORPWM, 255);
	
	stateVar = IDLE;
	subStateVar = ACT;
	configVar = FORWARD;
	
	Serial.println("RDY"); //tell raspi that setup is complete and we're ready to rock
}

void loop()
{
	//serial check
	String inString;
	char inChar;
	while(Serial.available())
	{
		delay(2); //tiny delay is necessary to clock in serial...
		inChar = Serial.read(); //get one character from buffer
		inString.concat(inChar); //concat single character to holding string so we can pass it to actionResponse.
	}
	actionResponse(inString); //acts and responds to serial
	
	//button check
	if(digitalRead(FWDBUTTON))
	{
		if(stateVar==IDLE)
		{
			configVar = FORWARD;
			stateVar = WORKING;
		}
	}
	if(digitalRead(REVBUTTON))
	{
		if(stateVar==IDLE)
		{
			configVar = REVERSE;
			stateVar = WORKING;
		}
	}
	
	switch(stateVar) //main switch statement
	{
		case IDLE: //not doing anything.
		{
			//TODO: fill in idle
		} break;
		
		case WORKING: //time to convey
		{
			switch(configVar) //check if configured for fwd or rev
			{
				case FORWARD:
				{
					switch(subStateVar) //switch between wait and act
					{
						case WAIT: //for waitin'
						{
							if(subWaitSentinel)
							{
								subWaitStart = millis();
								subWaitSentinel = false;
							}
							
							if((millis() - subWaitStart) >= subWaitTime) //if wait time has passed
							{
								subStateVar = ACT; //switch back to ACT loop
								subWaitSentinel = true; //set sentinel back to true for next invocation of wait state
							}
						} break;
						
						case ACT: //for doin' stuff
						{
							digitalWrite(MOTORENABLE, HIGH);
							digitalWrite(MOTOR1, HIGH);
							digitalWrite(MOTOR2, LOW);
							
							if(firstAct) //if just starting the action state
							{
								sensorTime = millis(); //save current time
								firstAct = false;
							}
							
							if(hasOccluded)
							{
								if(!digitalRead(BREAKBEAM)) //is cleared again
								{
									//Serial.println("cleared");
									digitalWrite(MOTOR1, LOW); //done. stop motor.
									
									//reset stuff
									hasOccluded = false;
									firstAct = true;
									
									stateVar = IDLE; //go to idle state.						
								}
								else //has not yet cleared
								{
									if((millis() - sensorTime) >= CLEAR_TIME) //sensor has not cleared before timeout, indicating jam
									{
										Serial.println("ERROR:CLEAR_TIME");
										
										//reset stuff
										hasOccluded = false;
										firstAct = true;
										
										stateVar = ERROR; //probably jammed.
										
									}
								}
							}
							else //hasOccluded sentinel not yet set
							{
								if(digitalRead(BREAKBEAM)) //is occluded
								{
									//Serial.println("occluded");
									hasOccluded = true;
									sensorTime = millis(); //reset sensorTime to current time.
								}
								else
								{
									if((millis() - sensorTime) >= OCCLUDE_TIME) //check to see if time to occlude has taken longer than allowed
									{
										Serial.println("ERROR:OCCLUDE_TIME");
										
										//reset stuff
										hasOccluded = false;
										firstAct = true;
										
										stateVar = ERROR; //probably jammed.
										
									}
									//restart loop.
								}
							}
						} break;
					}
				} break;
				
				case REVERSE:
				{
					switch(subStateVar) //switch between wait and act
					{
						case WAIT: //for waitin'
						{
							if(subWaitSentinel)
							{
								subWaitStart = millis();
								subWaitSentinel = false;
							}
							
							if((millis() - subWaitStart) >= subWaitTime) //if wait time has passed
							{
								subStateVar = ACT; //switch back to ACT loop
								subWaitSentinel = true; //set sentinel back to true for next invocation of wait state
							}
						} break;
						
						case ACT: //for doin' stuff
						{
							digitalWrite(MOTORENABLE, HIGH);
							digitalWrite(MOTOR1, LOW);
							digitalWrite(MOTOR2, HIGH);
							
							if(firstAct) //if just starting the action state
							{
								sensorTime = millis(); //save current time
								firstAct = false;
							}
							
							if(hasOccluded)
							{
								if(!digitalRead(BREAKBEAM)) //is cleared again
								{
									//Serial.println("cleared");
									digitalWrite(MOTOR2, LOW); //done. stop motor.
									
									//reset stuff
									hasOccluded = false;
									firstAct = true;
									
									stateVar = IDLE; //go to idle state.
								}
								else //has not yet cleared
								{
									if((millis() - sensorTime) >= CLEAR_TIME) //sensor has not cleared before timeout, indicating jam
									{
										Serial.println("ERROR:CLEAR_TIME");
										
										//reset stuff
										hasOccluded = false;
										firstAct = true;
										
										stateVar = ERROR; //probably jammed.
										
									}
								}
							}
							else //hasOccluded sentinel not yet set
							{
								if(digitalRead(BREAKBEAM)) //is occluded
								{
									//Serial.println("occluded");
									hasOccluded = true;
									sensorTime = millis(); //reset sensorTime to current time.
								}
								else
								{
									if((millis() - sensorTime) >= OCCLUDE_TIME) //check to see if time to occlude has taken longer than allowed
									{
										Serial.println("ERROR:OCCLUDE_TIME");
										
										//reset stuff
										hasOccluded = false;
										firstAct = true;
										
										stateVar = ERROR; //probably jammed.
										
									}
									//restart loop.
								}
							}
						} break;
					}						
				} break;
			}		
		} break;
		
		case ERROR:
		{
			//stop everything!
			digitalWrite(MOTOR1, LOW);
			digitalWrite(MOTOR2, LOW);
			digitalWrite(MOTORENABLE, LOW);
		} break;
	
		case ESTOP:
		{
			//stop everything!
			digitalWrite(MOTOR1, LOW);
			digitalWrite(MOTOR2, LOW);
			digitalWrite(MOTORENABLE, LOW);
		} break;
	}
}

int actionResponse(String inString) //act on serial commands and generate response
{
	//lots of ifs since can't switch Strings
	if(inString.equalsIgnoreCase("I"))
	{
		Serial.println(ID); //send ID to host
		return 0;
	}
	
	if(inString.equalsIgnoreCase("C0")) //configuration
	{
		if(stateVar == WORKING) //can't change configuration while working
		{
			Serial.println("WORKING");
			return 0;
		}
		else
		{
			Serial.println("C0");
			configVar = FORWARD;
			return 0;
		}

	}
	
	if(inString.equalsIgnoreCase("C1")) //configuration
	{
		if(stateVar == WORKING) //can't change configuration while working
		{
			Serial.println("WORKING");
			return 0;
		}
		else
		{
			Serial.println("C1");
			configVar = REVERSE;
			return 0;
		}
	}
	
	if(inString.equalsIgnoreCase("GO")) //init test command
	{
		if(stateVar == WORKING)
		{
			Serial.println("WORKING");
			return 0;
		}
		Serial.println("GO");
		stateVar = WORKING; //set next state to working
		//digitalWrite(GREEN_PIN, HIGH);
		return 0;
	}
	
	if(inString.equalsIgnoreCase("ESTOP"))
	{
		Serial.println("ESTOP");
		stateVar = ESTOP; //set next state to estop
		return 0;
	}
	
	/*if(inString.equalsIgnoreCase("RESULT"))
	{
		if(testResult == FAIL)
		{
			Serial.println("FAIL");
		}
		else if(testResult == PASS)
		{
			Serial.println("PASS");
		}
		else
		{
			Serial.println("UNKNOWN");
		}
	}*/
	
	if(inString.equalsIgnoreCase("STATE")) //status query
	{
		Serial.println("State, Config, subState:");
		Serial.println(stateVar);
		Serial.println(configVar);
		Serial.println(subStateVar);
		return 0;
	}
};

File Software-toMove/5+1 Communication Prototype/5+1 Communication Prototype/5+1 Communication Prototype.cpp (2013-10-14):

/*
 * _5_1_Communication_Prototype.cpp
 *
 * Created: 9/30/2013 2:53:20 AM
 *  Author: Nev
 */ 
#include "Arduino.h"
#include <string.h>
#include "CubeletsShield.h"

void setup();
void loop();

#include "Servo.h"

//Defines
#define ID "`0003"

#define PISTON_PIN 7 //pin to raise/lower piston. 
#define OPEN_PIN 5 //PWM servo pin to open/close faces
#define OPEN_POS 1 //degrees to send open servo for open
#define CLOSED_POS 180 //degrees to send open servo for close
#define START_PIN 9 //start button pin. Pulled from high to low when pressed.
#define RAISED_PIN A0 //pin to detect if arm is in raised position. must be set as INPUT_PULLUP, pulls LOW when raised.
#define RED_PIN 4
#define GREEN_PIN 6

#define SELECT_0 12 //LSB of select logic
#define SELECT_1 11 //middle bit of select logic
#define SELECT_2 10 //MSB of select logic


#define CAPTURE_PIN 8 //input capture pin
#define INTERRUPT_PIN 2 //interrupt pin

#define FAIL_THRESHOLD 100 //total number of individual connection failures allowed

Servo open;

long failCount = 0;
volatile int pinState = LOW;

void interruptServiceRoutine(void);

void setFace(unsigned int face);

void startTest(void);

void handleError(void);

enum State
{
	IDLE,
	WORKING,
	ERROR
	};
	
State stateVar = IDLE;

enum Result {UNKNOWN, FAIL, PASS};
Result testResult = UNKNOWN; //default unknown result

enum Error {NONE, RAISE_FAIL, LOWER_FAIL,};
Error errorVar = NONE;

int actionResponse(String inString);

CubeletsShield cubelets(true, 13);

void setup()
{
	Serial.begin(9600);
	Serial.println(ID);
	pinMode(PISTON_PIN, OUTPUT);
	pinMode(START_PIN, INPUT);
	pinMode(INTERRUPT_PIN, INPUT);
	pinMode(CAPTURE_PIN, INPUT);
	pinMode(SELECT_0, OUTPUT);
	pinMode(SELECT_1, OUTPUT);
	pinMode(SELECT_2, OUTPUT);
	pinMode(RAISED_PIN, INPUT_PULLUP);
	pinMode(RED_PIN, OUTPUT);
	pinMode(GREEN_PIN, OUTPUT);
	//open.attach(OPEN_PIN);
	//select face 1 for power whatever
	cubelets.initialize();
	digitalWrite(SELECT_0, LOW);
	digitalWrite(SELECT_1, HIGH);
	digitalWrite(SELECT_2, HIGH);
	digitalWrite(PISTON_PIN, HIGH); //raise piston when idle
	int startTime = millis();
	while(digitalRead(RAISED_PIN))
	{
		if((millis() - startTime) >= 2000)
		{
			errorVar = RAISE_FAIL;
			stateVar = ERROR;
			handleError();
			break;
		}
}
	open.attach(OPEN_PIN);
	open.write(OPEN_POS); //open faces
	delay(1000);
	open.detach();
	digitalWrite(GREEN_PIN, HIGH);
	Serial.println("RDY");
}

void loop()
{
	//serial check
	String inString;
	char inChar;
	while(Serial.available())
	{
		delay(2); //tiny delay is necessary to clock in serial...
		inChar = Serial.read(); //get one character from buffer
		inString.concat(inChar); //concat single character to holding string so we can pass it to actionResponse.
	}
	actionResponse(inString); //acts and responds to serial
	
	//button check
	if(!digitalRead(START_PIN))
	{
		if(stateVar == IDLE)
		{
			Serial.println("GO");
			stateVar = WORKING; //set next state to working
			startTest();
		}

	}
	
	//while(digitalRead(START_PIN)); //wait for start button to be pressed
	//Serial.println("GO");
}

void interruptServiceRoutine(void)
{
			failCount++;	
}

void setFace(unsigned int face)
{
	switch(face)
	{
		case 1:
		{
			digitalWrite(SELECT_0, LOW);
			digitalWrite(SELECT_1, LOW);
			digitalWrite(SELECT_2, LOW);
		} break;
		case 2:
		{
			digitalWrite(SELECT_0, LOW);
			digitalWrite(SELECT_1, LOW);
			digitalWrite(SELECT_2, HIGH);
		} break;
		case 3:
		{
			digitalWrite(SELECT_0, LOW);
			digitalWrite(SELECT_1, HIGH);
			digitalWrite(SELECT_2, LOW);
		} break;
		case 4:
		{
			digitalWrite(SELECT_0, LOW);
			digitalWrite(SELECT_1, HIGH);
			digitalWrite(SELECT_2, HIGH);
		} break;		
	}
}

int actionResponse(String inString) //act on serial commands and generate response
{
	//lots of ifs since can't switch Strings
	/*if(stateVar == ERROR);
	{
		Serial.println("ERROR"); //only do this. requires manual reset to clear error.
		return 0;
	}*/
	
	if(inString.equalsIgnoreCase("I"))
	{
		Serial.println(ID); //send ID to host
		return 0;
	}
	
	if(inString.equalsIgnoreCase("C0")) //configuration
	{
		if(stateVar == WORKING) //can't change configuration while working
		{
			Serial.println("WORKING");
			return 0;
		}
		else
		{
			Serial.println("C0");
			return 0;
		}

	}
	
	if(inString.equalsIgnoreCase("C1")) //configuration
	{
		if(stateVar == WORKING) //can't change configuration while working
		{
			Serial.println("WORKING");
			return 0;
		}
		else
		{
			Serial.println("C1");
			return 0;
		}
	}
	
	if(inString.equalsIgnoreCase("GO")) //init test command
	{
		if(stateVar == WORKING)
		{
			Serial.println("WORKING");
			return 0;
		}
		Serial.println("GO");
		stateVar = WORKING; //set next state to working
		startTest();
		//digitalWrite(GREEN_PIN, HIGH);
		return 0;
	}
	
	if(inString.equalsIgnoreCase("ESTOP"))
	{
		Serial.println("ESTOP");
		return 0;
	}
	
	if(inString.equalsIgnoreCase("RESULT"))
	{
		if(testResult == FAIL)
		{
			Serial.println("FAIL");
		}
		else if(testResult == PASS)
		{
			Serial.println("PASS");
		}
		else
		{
			Serial.println("UNKNOWN");
		}
	}
	
	if(inString.equalsIgnoreCase("STATE")) //status query
	{
		//Serial.println("State, Config, subState:");
		Serial.println(stateVar);
		return 0;
	}
};

void startTest(void)
{
	testResult = UNKNOWN;
	digitalWrite(RED_PIN, LOW);
	digitalWrite(GREEN_PIN, LOW); //clear both pins when result is unknown
	cubelets.stopAllCubeletCommunication();
	cubelets.greenOffAllCubelets();
	
	delay(50);
		
	digitalWrite(PISTON_PIN, LOW); //lower piston over cubelet
		
	long startTime = millis();
	while(!digitalRead(RAISED_PIN)) //wait for arm raised sensor to go HIGH, indicating that arm has dropped 
	{
		if((millis() - startTime) >= 2000) //if it doesn't drop in 2 seconds, something is wrong
		{
			stateVar = ERROR; //error handling here
			errorVar = LOWER_FAIL;
			handleError();
			return;
		}
	}
	
	delay(1000); //still want to wait a second to pass the drop		
		
	open.attach(OPEN_PIN);
	
	open.write(CLOSED_POS); //close faces
	
	delay(1000); //wait for faces to close
	
	open.detach();
	
	unsigned char testFace[5] = {2, 3, 4, 5, 1};
	
	delay(500); //response
	
	for(unsigned char face = 1; face <= 5; face++)
	{				 
// 		Serial.print("Starting comm on face ");
// 		Serial.println(face);
		cubelets.startCommunicationByFace(face);
		delay(1000);
// 		Serial.print("Setting face ");
// 		Serial.print(face);
// 		Serial.print(" to ");
// 		Serial.println(51*face);		
		while(cubelets.setBroadcastBlockValueByFace(face, 51*face) != 0); //keep trying until returns zero
/*		Serial.println("Set.");*/
		//cubelets.setBroadcastBlockValueByFace(face, 51*face);

		cubelets.greenOnByFace(face);
		
		delay(1000); //time for response
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

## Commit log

2013-09-29 Hooked up module names, position switching. Added skeleton for FarkusTable.Module Shortnames, remove/disconnect before searching again to prevent duplicates, and more
    [FarkusConfigureModuleWindow.py, FarkusDesk.py, FarkusGUIProcessGraphicManager.py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]
2013-09-29 Wired up part holder icons, static tests good.
2013-09-29 Hooked up Serial Number GUI. Bug fix on exit notifications
    [FarkusConveyance.py, FarkusDesk.py, FarkusGUIProcessGraphicManager.py]
2013-09-29 pause button replaced with advance and addpart
    [FarkusDesk.py]
2013-09-30 Statusbar hooked up. Some bug fixes. Message debug enabled.
    [FarkusConveyance.py, FarkusDesk.py, FarkusGUIProcessGraphicManager.py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]
2013-09-30 implemented dumb module control. Random part s/n, buttons disabled at times
2013-09-30 Reorganized menus, added logic to prevent opening module config if 0 connected
    [FarkusConfigureModuleWindow.py, FarkusDesk.py, FarkusModuleManager.py]
2013-10-02 Snapshot after 8/30 demo. Fixed module IDs
    [FarkusConveyance.py, FarkusModuleTypeManager.py]
2013-10-02 Added config var, functions to allow skipping intermediate conveyance positions
    [FarkusConveyance.py]
2013-10-03 double go command bug fixed
    [FarkusConveyance.py, FarkusDesk.py, FarkusGUIProcessGraphicManager.py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]
2013-10-03 Advance fixed, serialworker events hold FarkusModule object
    [FarkusConveyance.py, FarkusModule.py]
2013-10-14 Pre-surgery commit
    all my local stuff. prototype and running code. the only module running
    prototype code is the 5+1 Communication Prototype.
2013-10-14 re added the brightness tester prototype after removing it because apparently it was a submodule which is a thing.
2014-08-01 add cruzel hardware files
    [ACEnd_1032-Clevis.SLDPRT, AC_NM_0716x0102.SLDPRT, AC_PM_0716x0101.SLDPRT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]
2014-08-04 Initial commit of FARKUS Bench contents
    Includes FARKUS Bench components: Conveyance, Cubelet Holder, Electrical Interfaces, Modules, and Table. Also includes library feature for Cubelets connector in Design Library. Includes most mechanical hardware, electronics hardware, and software used on the FARKUS Bench. Missing some electronics hardware that is unfinished and certain pieces of software.
    [0169-ROBL-BOTTOM-ASSY.sldasm, 0169-ROBL-INNER_RING_02.sldprt, 0169-ROBL-LED_APTR3216_01.sldprt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]
2014-08-04 renamed crousel folder, moved arduino code to SW
    [ACEnd_1032-Clevis.SLDPRT, AC_NM_0716x0102.SLDPRT, AC_PM_0716x0101.SLDPRT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]
2014-08-04 renamed to FARKUS Crousel
    [ACEnd_1032-Clevis.SLDPRT, AC_NM_0716x0102.SLDPRT, AC_PM_0716x0101.SLDPRT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]
2014-08-04 crousel flashing module schematics and code.
    [Crousel-Pogobed-Motherboard-A.brd, Crousel-Pogobed-Motherboard-A.sch]

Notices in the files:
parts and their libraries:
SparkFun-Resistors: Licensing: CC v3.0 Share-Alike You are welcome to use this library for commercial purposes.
